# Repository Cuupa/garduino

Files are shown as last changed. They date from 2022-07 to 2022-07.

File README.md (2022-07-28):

# Disclaimer
This is a personal project done in my spare time. Use at your own risk.
The amazon links in the hardware section are affiliate links. You still pay the price you normally would, but I get a small commision if you buy something.

:warning: - Pay close attention

:construction: - Under construction. May change frequently and is not stable

# Goal
Since we don't have a power outlet on our balcony my requirements are that the system will work with a 5V DC Solar panel.

# Hardware
## Raspberry Pi 
I use an Raspberry Pi Zero W 1.1 as a gateway to fetch weather data.

[raspberrypi.com](https://www.raspberrypi.com/products/raspberry-pi-zero/)

## Arduino Micro
Board used for production. The micro will be soldered to the [PCB](#pcb) and will handle the sensor data and pumps.

[store.arduino.cc](https://store.arduino.cc/products/arduino-micro)

## WayinTop 3 3V-5V pumps :warning:
Not the best pumps, but rather cheap and used for prototyping.
They don't seem have insulation to protect the electronics from the water, so use at your own risk.
You'd better buy a more expensive one, but I didn't know better and wanted some cheap pumps for prototyping.

(source: https://youtu.be/GNNzLwCidCE?t=250)

[amazon](https://amzn.to/3OmWYmE)

## 5V DC submergeable pump
I use this pump as a more reliable pump to water the plants

[amazon](https://amzn.to/3o1D1Gq)

## Elegoo 4 channel 5V DC relay
Be aware that LOW seems to activate the relay instead of HIGH. The code is written that way. If you use a different relay, you might want to change that. 

Also see [Changes you probably have to make - Relay](#relay)

[amazon](https://amzn.to/3NtVxl7)

## KeeYees capacitive hygrometers 
[amazon](https://amzn.to/3OEAihn)

## Waterproof case
If you use an arduino uno and a standard sized raspberry pi like a Pi 4 this case is definitely to small.
[amazon](https://amzn.to/3IxMej0)

## Cables
## USB-extension for the pump.
Since the pump uses 5V DC over USB and the controller is somewhat far away of the water reservoir and the pump, I use these as an extension cord.

[amazon](https://amzn.to/3P59U0J)

## PCB
I designed the PCB using [easyeda](https://easyeda.com).

The final circuit board looks something like this:



All files including Gerber files can be found here: [docs/PCB/](docs/PCB/)
I had to order at least 5 PCBs which costs me around 8$ (including shipping).

# Software
The software in this git repository is as of now a simple prototype and is under active development.

If you want to use the software for yourself feel free to change it to match your needs.

## Dependencies
- AUnit [documentation](https://www.arduino.cc/reference/en/libraries/aunit/)
- LowPower [documentation](https://github.com/rocketscream/Low-Power)
- ArduinoJson [documentation](https://arduinojson.org/)
## Changes you probably have to make

### Hygrometers and pumps
In ```IrrigationSystem.h``` theres a section which probably looks like this:

``` C++
    static const int numberOfIrrigationSystems = 2;

    SensorPumpPair sensorPumpPair[numberOfIrrigationSystems];

    Placement placements[numberOfIrrigationSystems] = {
        Placement::OUTSIDE_ROOFED,
        Placement::INSIDE};

    WaterRequirement waterRequirements[numberOfIrrigationSystems] = {
        WaterRequirement::HIGH_WATER_REQUIREMENTS,
        WaterRequirement::MEDIUM_WATER_REQUIREMENTS};

    //  key-value pairs of every sensor-pump-pair
    //  Each entry will be an irrigation system
    const byte addresses[numberOfIrrigationSystems][2] = {
        {A0, 11},
        {A1, 12}};

    int sensorAirValues[numberOfIrrigationSystems] = {590, 130};
    int sensorWaterValues[numberOfIrrigationSystems] = {285, 90};
```
The first line is the number of irrigation systems. Unfortunately, I'm a java, not a c++ dev, so I did not manage to find a more elegant solution... yet

Change the number to the number of your irrigation systems, watering loops whatever you call it. Following, there's where you placed your plants and then, what the water requirements are. 

Then, there's the addresses of your sensor-pump-pairs.

The first value of these key-value-pairs is the analog pin which the sensor is connected to, the second value the digital pin, for the pump.

Sensor on ```A0``` activates the pump on pin ```11``` if necessary, sensor on ```A1``` acitvates pump on pin ```12``` and so on. 

The three fields ```placement```, ```waterRequirements``` and ```addresses``` corresponds one another, so keep attention to the order of your values.

For example sensor-pump-pair number one (or at index 0 to be precise) reads as follows:

Sensor at ```A0```

Pump at ```11```

Placement ```outside-roofed```

Water requirements ```high-water-requirement```

### Relay
In ```Pump.cpp``` there's an ```init```-Function. The relay I use seems to be off on ```HIGH``` and on on ```LOW```. Depending on the relay you use, you might want to change that.

### Hygrometer calibration
Depending on your assembly the hygrometers can return different values.
During my prototyping sensor 1 returned a value of around 600, while sensor 2 returned a value around 130 while both being exposed to air.

I already provided a simple program for finding the base values of the sensor.

Open the ```Hygrometer-Calibration.ino``` and change the analog input to the pin you connected the hygrometer to. Or just leave it and connect the sensor to A0 :D

When you start the program, it first measures the "air-value" (so leave the sensor lying on your table or something). Then you have a 5 second pause to place the sensor in a glass of water. It then measures the "water-value" and logs it to the serial console.

Copy these two values and change the two lines named ```sensorAirValues``` and ```sensorWaterValues``` in file ```IrrigationSystem.h``` accordingly.

``` C++
const int sensorAirValues[] = {600, 130};
const int sensorWaterValues[] = {290, 90};
```

In this example I have two sensors. Sensor 1 has an air-value of 600 and a water-value of 290, while sensor 2 has 130 and 90 accordingly.

Repeat these steps for every sensor you have.

This is neccessary to calculate the moisture percentage.

### Water level measurement :construction:

### Communicating with a gateway
If you use a rapsberry pi gateway like I do, change the ```connectedToServer``` to ```true```. This constant is located in ```Main.h```

### Weather data
There is a directory called ```Raspberry Pi``` where are scripts for setting up your pi. Be sure to perform the step at [Communicating with a gateway](#Communicating with a gateway)

Open ```setup_communication.sh```and change the username matching your system. In my case it's called garduino. Then run these steps.

Then copy the ```server.py```, ```influxdb.config``` and ```weather.config``` to your pi to a directoy you might seem fit (like ```/opt/garduino/```). Change the values in the config to match your needs.

As soon you start the ```server.py```(```python3 sever.py```), it listens to any incoming request over serial.

### Grafana monitoring :construction:
If you want to visualize the data gathered by the sensors there is a script called ```setup_monitoring.sh```.

Set your credentials and run the script to install influxdb and grafana.

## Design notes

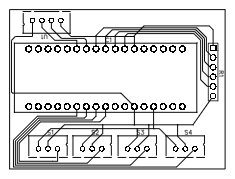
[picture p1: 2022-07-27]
docs/PCB/PCB.png

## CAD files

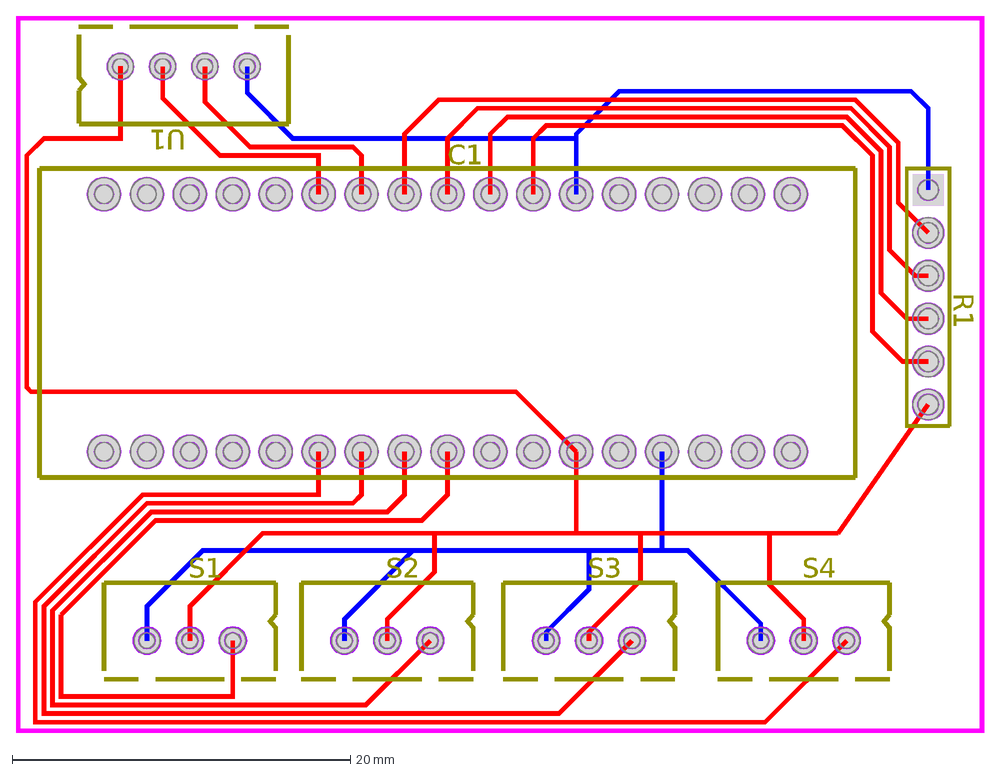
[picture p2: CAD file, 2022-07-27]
docs/PCB/PCB.dxf
C1
S1
S2
S3
S4
R1
U1

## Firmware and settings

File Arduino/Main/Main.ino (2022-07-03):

/*

*/
#include "Message.h"
#include "Main.h"
#include "Debug.h"
#include "PowerSaving.h"
#include "WaterLevelMeasurement.h"
#include "WaterDetermination.h"
#include "IrrigationSystem.h"

int numberOfIrrigationSystems = -1;

IrrigationSystem irrigationSystem;
Message message;

void setup()
{
  delay(1000);
  Serial.begin(BAUD_RATE);
  // Serial.setTimeout(5000);

  debug(VERSION_NUMBER);

  numberOfIrrigationSystems = (sizeof(irrigationSystem.sensorPumpPair) / sizeof(*irrigationSystem.sensorPumpPair));
  debug(String(numberOfIrrigationSystems) + " Sensor-Pump pairs found");
  delay(10000);
}

void loop()
{
  String weatherData[] = {};
  debug("Requesting weather data");
  message.request(RequestType::WEATHER_DATA, weatherData);

  debug("Received weather data");
  debug(weatherData);

  bool isRaining = isCurrentlyRaining(weatherData);
  bool isRainfallSufficiant = isTodaysAndTomorrowsRainfallSufficient(weatherData);
  Evaporation evaporation = getEvaporation(weatherData);

  debug("It's raining: " + String(isRaining));
  debug("Rainfall is sufficiant: " + String(isRainfallSufficiant));

  // iterate over every sensor
  for (int systemIndex = 0; systemIndex < numberOfIrrigationSystems; systemIndex++)
  {
    if (irrigationSystem.isPlantOutside(systemIndex) && (isRaining || isRainfallSufficiant))
    {
      continue;
    }

    float sensorValue = irrigationSystem.getMoistureSensorValue(systemIndex);

    if (!isHygrometerOkay(sensorValue, systemIndex))
    {
      continue;
    }

    int soilMoisturePercent = irrigationSystem.getSensorValueInPercent(sensorValue, systemIndex);
    message.sendNotification(HygrometerStatus::HYGROMETER_OK, soilMoisturePercent, systemIndex);

    float waterlevel = getWaterLevelInLiter();
    float waterlevelPercentage = convertLiterToPercent(waterlevel);

    if (!isWaterLevelOkay(waterlevel, waterlevelPercentage))
    {
      continue;
    }

    float waterlevelBefore = waterlevel;
    while (irrigationSystem.needsWatering(systemIndex, soilMoisturePercent))
    {
      waterlevel = getWaterLevelInLiter();
      waterlevelPercentage = convertLiterToPercent(waterlevel);

      if (!isHygrometerOkay(sensorValue, systemIndex))
      {
        break;
      }

      if (!isWaterLevelOkay(waterlevel, waterlevelPercentage))
      {
        break;
      }

      irrigationSystem.pump(2000, systemIndex);
      sensorValue = irrigationSystem.getMoistureSensorValue(systemIndex);
      soilMoisturePercent = irrigationSystem.getSensorValueInPercent(sensorValue, systemIndex);
    }

    float newWaterlevel = waterlevel;
    if (newWaterlevel < waterlevelBefore)
    {
      message.sendNotification(waterlevelBefore - newWaterlevel, systemIndex);
    }
  }

  int sleepTimeInMinutes = 60;
  if (evaporation == Evaporation::LOW_EVAPORATION)
  {
    // sleep 3h
    sleepTimeInMinutes = 180;
  }

  else if (evaporation == Evaporation::MEDIUM_EVAPORATION)
  {
    // sleep 1h
    sleepTimeInMinutes = 60;
  }

  else if (evaporation == Evaporation::HIGH_EVAPORATION)
  {
    // sleep 30 min
    sleepTimeInMinutes = 30;
  }
  sleep(sleepTimeInMinutes);
}

bool isHygrometerOkay(float sensorValue, int sensorIndex)
{
  if (!irrigationSystem.isSensorInSoil(sensorValue, sensorIndex))
  {
    message.sendNotification(HygrometerStatus::HYGROMETER_OUT_OF_SOIL, 0, sensorIndex);
    return false;
  }

  if (!irrigationSystem.isSensorConnected(sensorValue))
  {
    message.sendNotification(HygrometerStatus::HYGROMETER_NOT_CONNECTED, 0, sensorIndex);
    return false;
  }
  return true;
}

bool isWaterLevelOkay(float waterlevel, float waterlevelPercentage)
{
  if (isWaterLevelDisabled())
  {
    message.sendNotification(Waterlevel::WATER_LEVEL_DISABLED, waterlevel);
    return true;
  }

  if (isWaterLevelCritical(waterlevelPercentage))
  {
    message.sendNotification(Waterlevel::WATER_LEVEL_CRITICAL, waterlevel);
    return false;
  }

  else if (isWaterLevelLow(waterlevelPercentage))
  {
    message.sendNotification(Waterlevel::WATER_LEVEL_LOW, waterlevel);
    return true;
  }

  else
  {
    message.sendNotification(Waterlevel::WATER_LEVEL_OK, waterlevel);
    return true;
  }
}

Evaporation getEvaporation(String weatherData[])
{
  if (weatherData[0].equals("ok"))
  {
    String evaporationString = weatherData[4];
    if (evaporationString == "low")
    {
      return Evaporation::LOW_EVAPORATION;
    }

    else if (evaporationString == 'medium')
    {
      return Evaporation::MEDIUM_EVAPORATION;
    }
    else if (evaporationString == 'high')
    {
      return Evaporation::HIGH_EVAPORATION;
    }
  }
  // No data. Returning medium as default
  return Evaporation::MEDIUM_EVAPORATION;
}

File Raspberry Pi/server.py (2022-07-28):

#!/usr/bin/env python3

import serial
import json
import requests
import time

from influxdb import InfluxDBClient
from bs4 import BeautifulSoup
from datetime import datetime

from os.path import exists

# Constants
_utf_8 = 'utf-8'

_weather_config_file = 'weather.config'
_influx_config_file = 'influxdb.config'

# weather config constants
_zip_code = 'zip_code'

# Influxdb config file constants
_influx_host = 'influx_host'
_influx_port = 'influx_port'
_influx_username = 'influx_username'
_influx_password = 'influx_password'
_influx_database_name = 'influx_database_name'


# Payload constants

# Requests
_type = 'type'
_measurement = 'measurement'
_request = 'request'
_weather_data = 'weather-data'

_water_level = 'water-level'
_hygrometer_status = 'hygrometer-status'
_watered_volume = 'watered-volume'
_hygrometer = 'hygrometer'
_humidity = 'humidity'
_system_name = 'system-name'
_sensor_index = 'sensor-index'
_liter = 'liter'
_watered = 'watered'

# influx
_tags = 'tags'
_time = 'time'
_fields = 'fields'

# agrarwetter
_agrarwetter_current_conditions_selector = '.MITTEFORMULARSPALTE_WETTER > .SCHRIFT_FORMULAR_WERTE_MITTE'
_rainfall_selector = 'tr', {'id': 'NS_24H'}
_evaporation_selector_1 = 'tr', {'id': 'VERDUNST'}
_evaporation_selector_2 = '.SCHRIFT_FORMULAR_WERTE_MITTE'
_span = 'span'

_temperature = 'temperature'
_condition = 'condition'
_evaporation = 'evaporation'
_rainfall_today = 'rainfall-today'
_rainfall_tomorrow = 'rainfall-tomorrow'

_gering = 'gering'
_maessig = 'mäßig'
_hoch = 'hoch'

_low = 'low'
_medium = 'medium'
_high = 'high'

_sonnig = 'sonnig'
_heiter = 'heiter'
_klar = 'klar'
_bedeckt = 'bedeckt'
_wolkig = 'wolkig'
_stark_bewoelkt = 'stark bewölkt'
_regen = 'regen'
_sunny = 'sunny'
_bright = 'bright'
_cloudy = 'cloudy'
_very_cloudy = 'very_cloudy'
_rain = 'rain'


input_device = '/dev/ttyACM0'

influx_client = None

zip_code = ''

weather_url = 'https://www.proplanta.de/Wetter/profi-wetter.php?SITEID=60&PLZ={zip_code}&WETTERaufrufen=plz&Wtp=&SUCHE=Wetter&wT='
weather_request_header = {
    'User-Agent': 'Mozilla/5.0 (Windows NT 10.0; Win64; x64) AppleWebKit/537.36 (KHTML, like Gecko) Chrome/103.0.0.0 Safari/537.36',
    'Accept-Encoding': 'gzip,deflate,sdch'
}

debug = True


def readWeatherConfig():
    zip = ''
    
    if not exists(_weather_config_file):
        error(_weather_config_file + ' does not exist.')

    with open(_weather_config_file) as f:
        for line in f:
            values = line.split('=')
            key = values[0].strip()
            value = values[1].strip()
            if key == _zip_code:
                zip = value
    return zip


def readInfluxConfig():
    influx_host = ''
    influx_port = 0
    influx_username = ''
    influx_password = ''
    influx_database_name = ''

    if not exists(_influx_config_file):
        error(_influx_config_file + 'does not exist.')

    with open(_influx_config_file) as f:
        for line in f:
            values = line.split('=')
            key = values[0].strip()
            value = values[1].strip()
            if key == _influx_host:
                influx_host = value
            elif key == _influx_port:
                influx_port = value
            elif key == _influx_username:
                influx_username = value
            elif key == _influx_password:
                influx_password = value
            elif key == _influx_database_name:
                influx_database_name = value

    return influx_host, influx_port, influx_username, influx_password, influx_database_name


def setup():
    influx_host, influx_port, influx_username, influx_password, influx_database_name = readInfluxConfig()

    if not influx_host:
        try:
            global influx_client
            influx_client = InfluxDBClient(host=influx_host,
                                    port=influx_port,
                                    username=influx_username,
                                    password=influx_password,
                                    ssl=False,
                                    verify_ssl=False)

            databases = influx_client.get_list_database()

            database_exists = next((item for item in databases if item['name'] == influx_database_name), False)
            
            if not database_exists:
                influx_client.create_database(influx_database_name)
            influx_client.switch_database(influx_database_name)
        except ConnectionError as ce:
            error('Could not connect to influxdb')
            error(ce)
    global zip_code
    zip_code = readWeatherConfig()


def connect():
    while 1:
        try:
            ser = serial.Serial(input_device, 9600, timeout=5)
            ser.reset_input_buffer()
            return ser
        except:
            debug('Device not connected')


def listen():
    ser = connect()
    debug('listening')
    while 1:
        try:
            if ser.in_waiting > 0:
                message = ser.readline().decode(_utf_8).rstrip()
                debug('Received message')
                debug(message)
                if "Debug: " in message:
                    continue

                payload = json.loads(message)
                request_type = payload[_type]

                if request_type == _measurement:
                    if influx_client is not None:
                        json_payload = formatMeasurementDataForInflux(payload)
                        influx_client.write_points(json_payload)
                elif request_type == _request:
                    if payload[_request] == _weather_data:
                        weather = getWeatherData()
                        response = json.dumps(weather)
                        formatWeatherDataForInflux(response)
                        debug("Response")
                        debug(response)
                        ser.write(response.encode(_utf_8))
        except IOError as ioe:
            ser = connect()
        except Exception as e:
            debug(e)
            debug('failed to process ' + message)


def formatWeatherDataForInflux(response):
    pass
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

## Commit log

2022-06-22 first commit of the main program with two sensors and two pumps just to tinker a little bit
2022-06-22 little calibration program for the moisture sensor
2022-06-22 fixed sensor in soil detection
2022-06-23 gitignore to ignore arduino libs
2022-06-24 waterlevel measurement and changes for arduino micro
2022-06-24 currently disabled
2022-06-24 powersaving works different for arduino micro
2022-06-26 check if rain is sufficiant. in that case don't water
2022-06-27 added response to arduino
2022-07-27 documentation and gerber files
    [Autorouter_PCB.dsn, PCB.dxf]
